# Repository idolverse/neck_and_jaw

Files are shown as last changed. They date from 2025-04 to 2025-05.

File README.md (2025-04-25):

<h1>颈部和下颌的组装</h1>

好的，我想你的躯干应该已经组装好了，或者差不多了。颈部的组装应该不会太难。用到的伺服器都不需要改装，可以直接设置。太棒了。

从图库下载 STL(已下载)

在打印所有部件之前，您应该打印一份校准器 (CALIBRATOR)，以检查部件是否能够拼合。如果您在拼合这些部件时遇到困难，可以调整切片软件的水平扩展设置来解决这个问题。此设置可能因切片机和打印机而异，但用户报告称，将其设置为 -0.15 是一个不错的起点。

填充率为 30%，壁厚为 2.5 毫米，最好无筏，无支撑（除非另有说明），大部件使用边缘以避免翘曲。

注意：我设计了一种新的颈部机制，可以在图库中下载，但未在下面的教程中显示。（见newNeck.mp4）

以下是颈部和下颌所需的零件清单和打印数量：

1x JawHinge

1x JawHinge

1x JawPiston

1x JawSupport

1x Jaw

1x LowBack

1x FaceHolder

1x GearHolder

1x MainGear

1x NeckBolts

1x NeckHinge

1x Neck

1x Ring

1x ServoGear

1x SkullServoFix

1x ThroatHolder

1x ThroatHole

1x ThroatPistonBase

1x ThroatPiston



将“MainGear”用胶水或螺丝固定到“NeckHinge”上



使用“GearHolder”并将“ServoGear”安装到其中。将随 HS-805BB 舵机一起提供的执行器轮拧到“ServoGear”上。



使用您的 Arduino 板并将您的 HS-805BB 伺服设置为 90°。
将其推入转盘。



这有点棘手，但可以用螺丝刀上的磁铁来实现。使用舵机附带的螺丝，将转盘拧到“ServoGear”内的舵机上。保持舵机呈90°。



将此组件安装到“MainGear”和“NeckHinge”组件上，并使用一些润滑脂以减轻旋转。“GearHolder”应与“NeckHinge”对齐，并且伺服器应保持90°。



将“LowBackRight”和“LowBackLeft”或“Temporary”固定到“GearHolder”。这将是头骨的后部。



将“Ring”拧到“MainGear”上。尽量避免零件之间松弛。



使用您最喜欢的钳子来安装“FaceHolder”。
您可以安装它们两个。



现在我们来制作下巴。取“JawPiston”并将其旋转到“JawHinge”内部，直到它们之间偏移1cm。



将此螺丝安装到 HK15298 或类似舵机的转盘上。使用 Arduino 开发板将舵机设置为 0°。保持 1cm 的偏移，“JawHinge” 应与舵机成 90° 角安装。



将螺丝“SkullServoFix”安装在 HS-805BB 伺服器上。



把4个螺丝全部拧上。别介意我照片上的电线，它们来自相机。



用丙酮将两个“JawHolders”粘在整个组件的两侧。它与“FaceHolders”贴合。



现在取出您的 HK15298 组件并将其滑过。



拧上所有 4 颗螺丝，固定您的 HK15298 伺服器。



移除“Jaw”的预支撑。图片上显示的“Jaw”只是一半。这是我之前做的测试打印。你的“Jaw”是一体式打印。



将“Jawsupport”拧到“Jaw”上。确保“Jawsupport”的平面朝内。



修复“ThroatHole”的问题。我的看起来和你的不一样。抱歉，图片显示“ThroatPiston”和“ThroatPistonBase”应该还没有安装，后续步骤会安装。



将“Neck”拧到“ThroatHole”上。



用 8 毫米螺栓将“NeckHinge”固定到“Neck”上（或从手上打印一个）
假设您已将 HS-805BB 舵机固定在躯干组件中。使用 Arduino 开发板将舵机旋转 90°。稍微旋转“ThroatPiston”和“ThroatPistonBase”，使“NeckHinge”平直。



将“ThroatPiston”拧到转盘上，使伺服器保持 90°。



用 8 毫米螺栓将“ThroatPistonBase”固定到“NeckHinge”（或从手上打印一个）
现在，当伺服电机从 0 度旋转到 180 度时，整个头部应该能够上下移动。用 arduino 进行测试。请仔细运行此测试。



将头部抬起，将下颌组件滑入头部。



将“JawSupports”穿过并安装到“JawHinges”和“JawHolders”上



使用垫圈，固定螺丝。

使用 Arduino 对钳口机构进行测试。

注意：钳口伺服器只能旋转 0 到 20°（我估计），如果旋转超过 20° 可能会损坏零件。请自行测试。（目前我记不清我的伺服器具体能旋转到多少度了。等我重新插上电源后再解决这个问题。）

您可以在“Neck”中运行伺服器的电缆。

现在您应该可以通过 Arduino 移动头部和下巴了。

将 MyRobotLab 与InMoov.minimalHead.py结合使用：https://github.com/MyRobotLab/pyrobotlab/blob/develop/service/InMoovHead.py

检查InMoov 服务 Myrobotlab的引脚连接以将其添加到您的机器人。

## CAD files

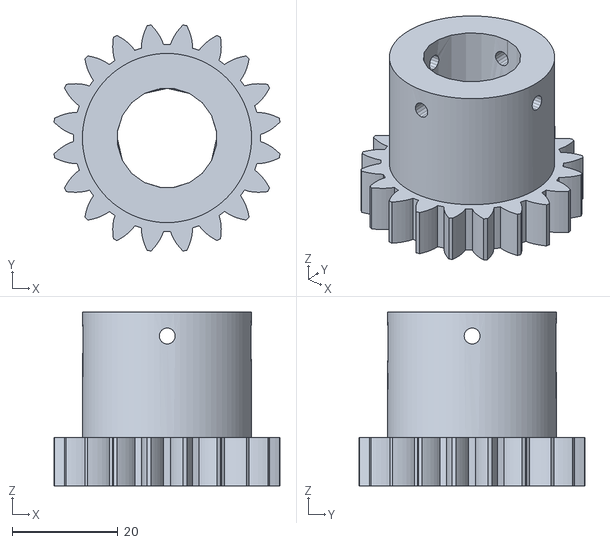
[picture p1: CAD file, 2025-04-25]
颈部和下颌STL/颈部STL/MainGearV2.stl
42.7 x 42.7 x 32.8

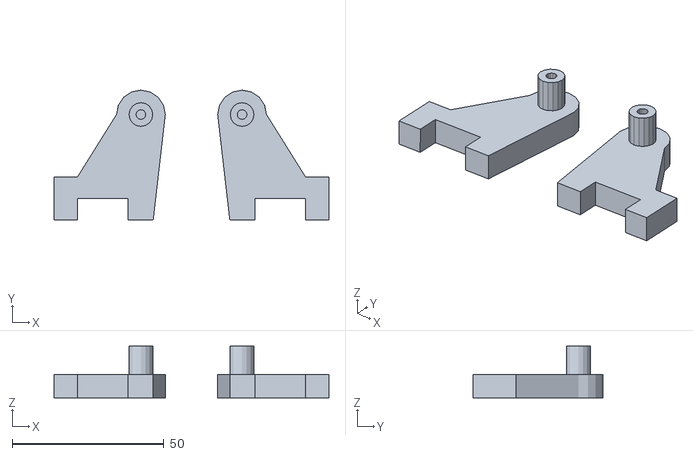
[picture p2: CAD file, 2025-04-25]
颈部和下颌STL/脸部和下颌STL/JawHingeV3.stl
90.5 x 42.7 x 17.0

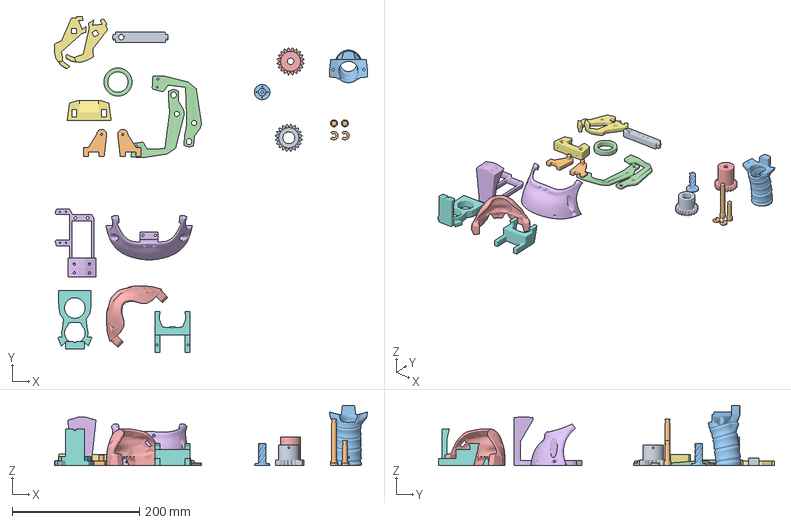
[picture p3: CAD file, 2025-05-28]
颈部和下颌STL/颈部-.3mf
492.9 x 528.6 x 94.9 mm
JawHingeV1.stl
JawHingeV3.stl
JawPistonV1.stl
JawSupportV1.stl
JawV4.stl
LowBackV5.stl
FaceHolderV4.stl
GearHolderV2.stl
MainGearV2.stl
NeckBoltsV2.stl
NeckV3.stl
RingV2.stl
ServoGearV2.stl
SkullServoFixV1.stl
ThroatHolderV2.stl
ThroatHoleV3.stl

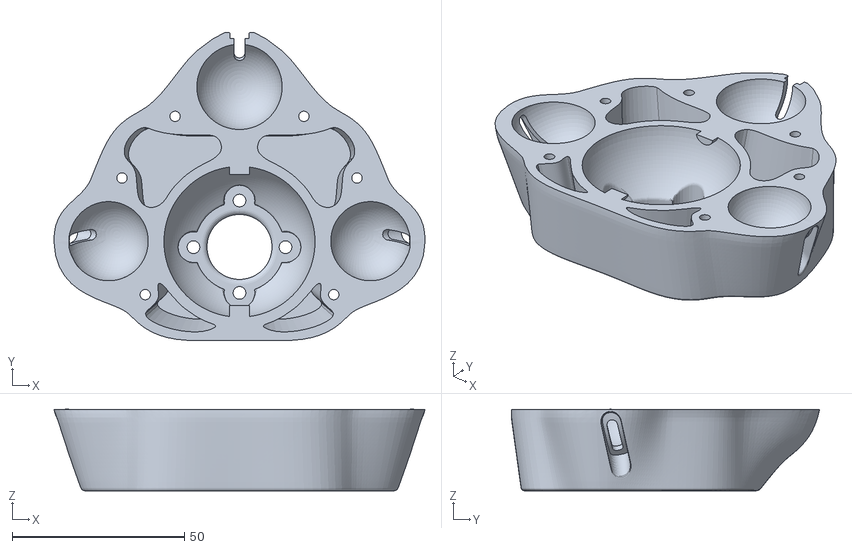
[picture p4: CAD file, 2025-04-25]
颈部和下颌STL/颈部STL/NeckPlateHighV2.stl
107.5 x 89.4 x 23.7

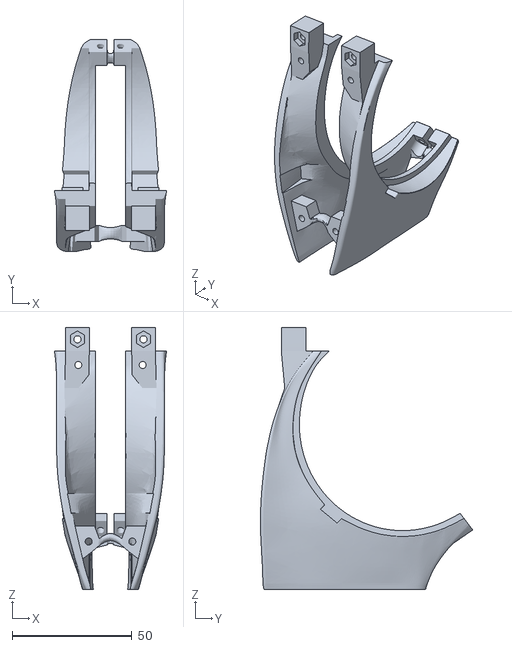
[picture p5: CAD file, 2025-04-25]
颈部和下颌STL/脸部和下颌STL/SideHearV5.stl
46.8 x 88.6 x 109.3

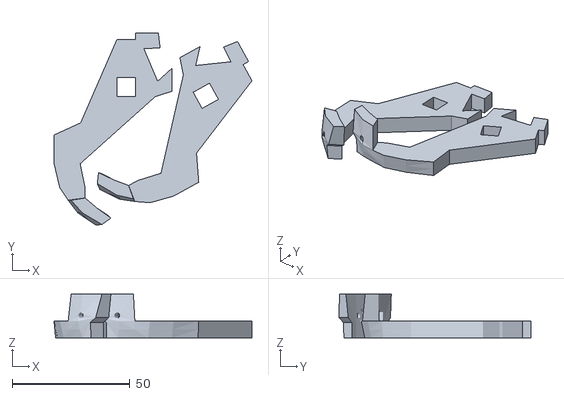
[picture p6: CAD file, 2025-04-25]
颈部和下颌STL/颈部STL/FaceHolderV4.stl
84.1 x 81.6 x 18.6

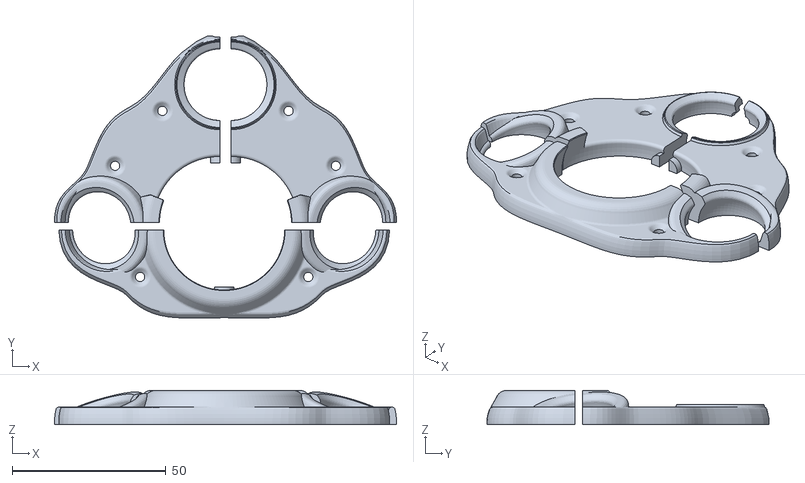
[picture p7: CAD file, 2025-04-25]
颈部和下颌STL/颈部STL/NeckPlateV2.stl
111.4 x 91.9 x 11.1

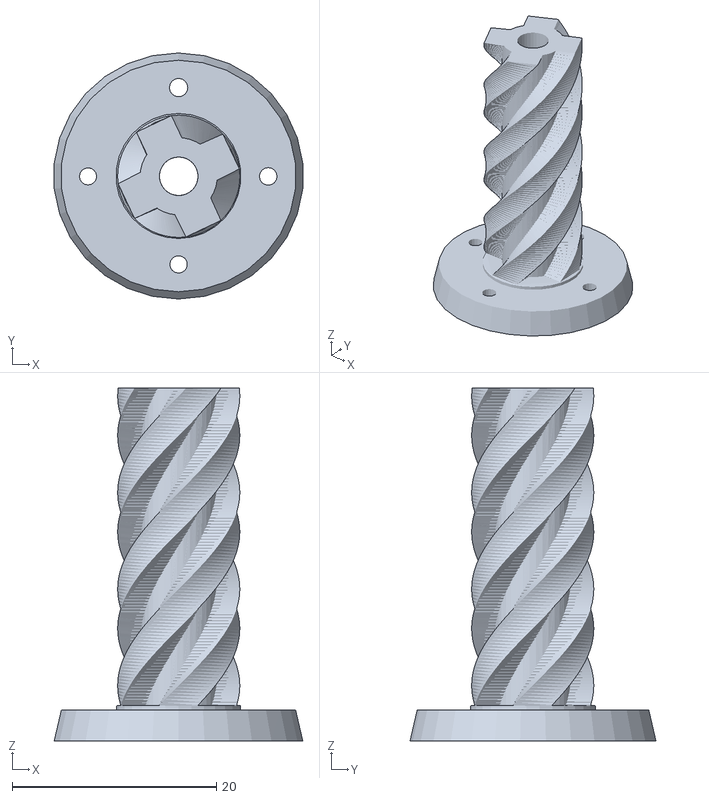
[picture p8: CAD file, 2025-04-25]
颈部和下颌STL/脸部和下颌STL/JawPistonV1.stl
24.4 x 24.1 x 34.6

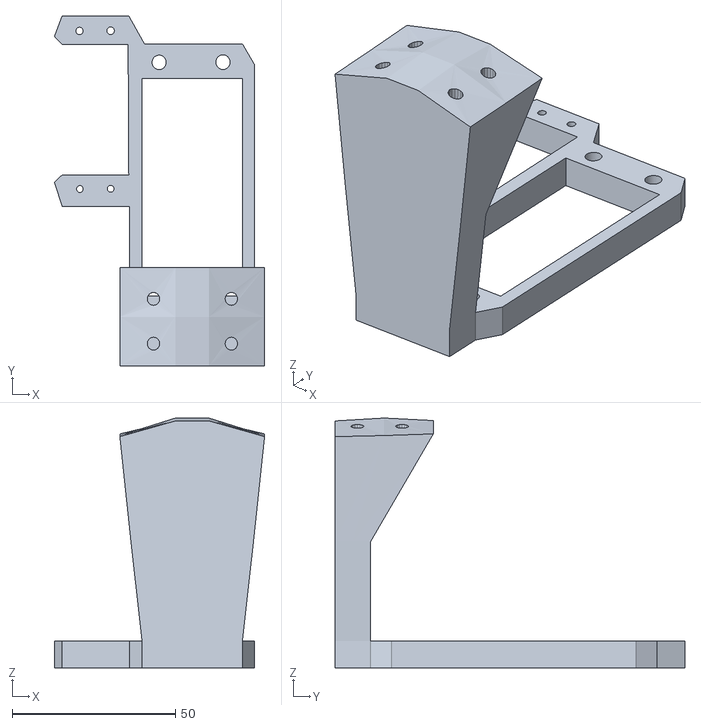
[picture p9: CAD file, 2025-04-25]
颈部和下颌STL/颈部STL/SkullServoFixV1.stl
64.5 x 107.4 x 76.7

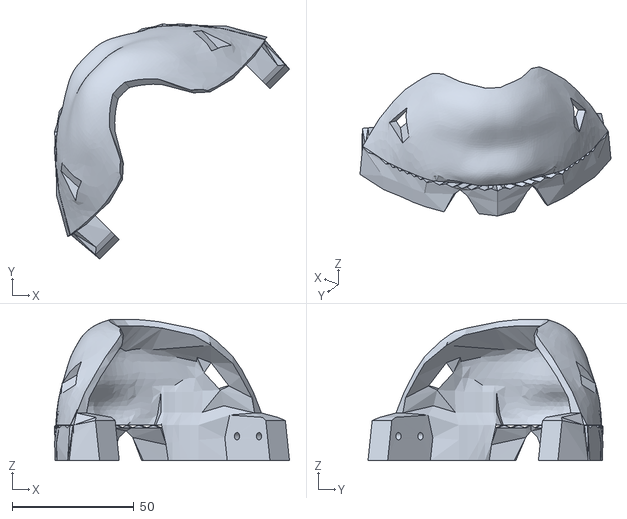
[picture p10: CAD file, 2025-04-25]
颈部和下颌STL/脸部和下颌STL/JawV4.stl
96.4 x 96.4 x 58.0

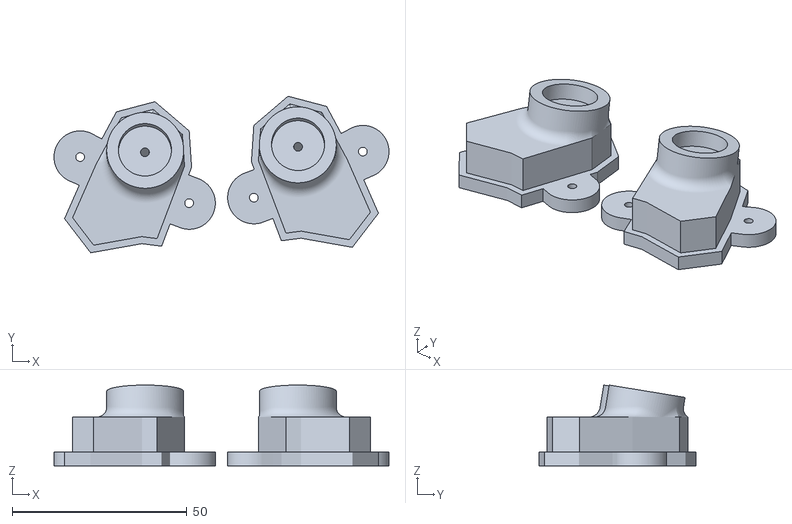
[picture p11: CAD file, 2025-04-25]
颈部和下颌STL/颈部STL/NeckServoPivotV2.stl
96.0 x 44.9 x 23.2

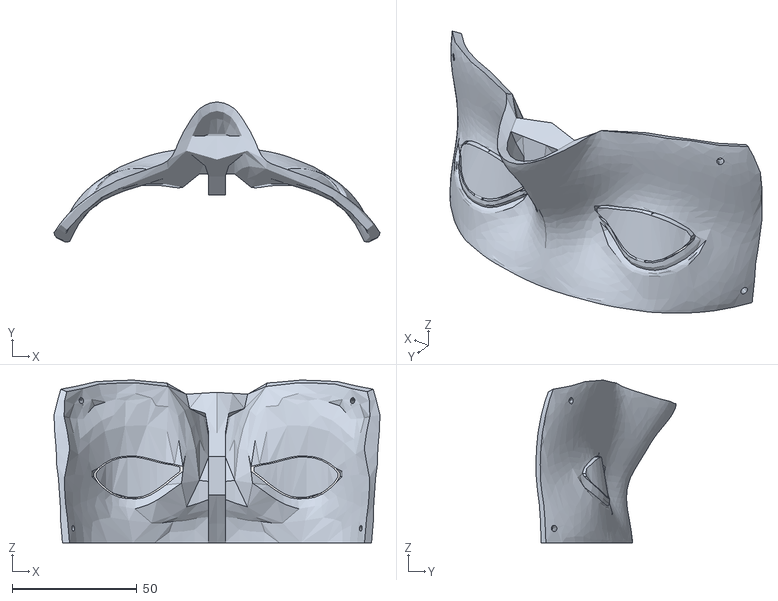
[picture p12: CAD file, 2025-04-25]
颈部和下颌STL/脸部和下颌STL/EyeglassV4.stl
130.6 x 56.1 x 65.2

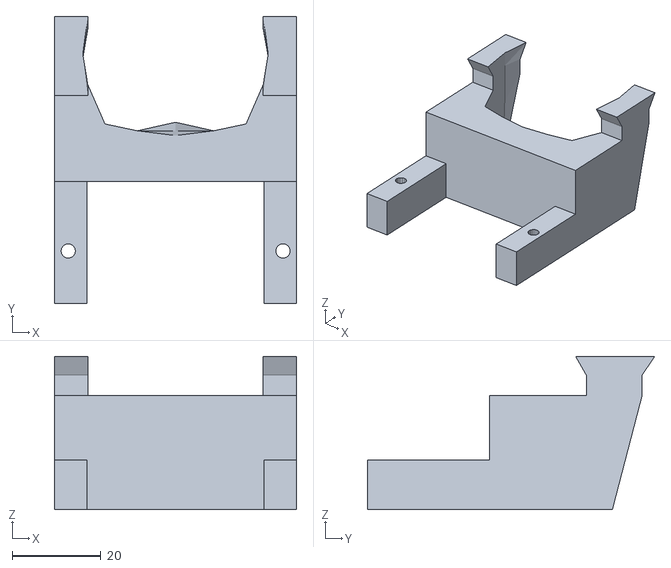
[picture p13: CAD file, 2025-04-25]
颈部和下颌STL/颈部STL/ThroatHoleV3.stl
54.6 x 64.8 x 34.6

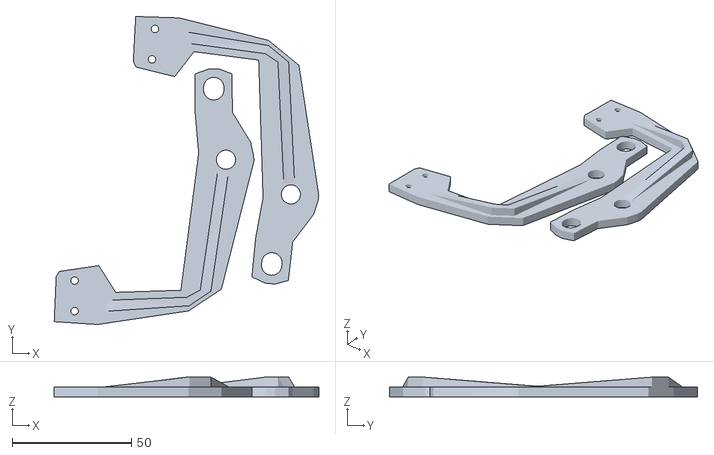
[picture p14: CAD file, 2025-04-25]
颈部和下颌STL/脸部和下颌STL/JawSupportV1.stl
110.8 x 128.9 x 8.26

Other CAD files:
颈部和下颌STL/颈部STL/ThroatHolderV2.stl
颈部和下颌STL/颈部STL/ServoGearV2.stl
颈部和下颌STL/颈部STL/NeckPistonV2.stl
颈部和下颌STL/颈部STL/SpeakerMouthHolderV2.stl
颈部和下颌STL/脸部和下颌STL/JawHingeV1.stl
颈部和下颌STL/颈部STL/GearHolderV2.stl
颈部和下颌STL/颈部STL/NeckBoltsV2.stl
颈部和下颌STL/颈部STL/NeckJointLowerV5.stl
颈部和下颌STL/颈部STL/NeckPistonBaseFrontV1.stl
颈部和下颌STL/颈部STL/NeckPistonFrontV2.stl
颈部和下颌STL/颈部STL/NeckPistonSideV1.stl
颈部和下颌STL/颈部STL/NeckServoHolderV2.stl
颈部和下颌STL/颈部STL/PistonBaseSideV2.stl
颈部和下颌STL/颈部STL/RingV2.stl
